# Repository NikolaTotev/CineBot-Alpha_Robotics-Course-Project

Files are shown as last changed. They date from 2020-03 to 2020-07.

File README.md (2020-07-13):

# Project Cinebot Alpha

This is the documentation for my Robotics Course Project created during my second year, second semester in FMI for the course Practical Robotics and Smart "Things".

<p align="center">
Robot_Full
</p>

## *Acknowledgements*
Before I begin, I would like to acknowledge my parents, for their constant love and encouragement, not only for this project but for all of my previous and current endeavors. Without them, this project would not be the same.
I would also like to thank the teachers of the teachers that guided me
through the skills I needed to learn to make this project a reality. In no particular order I'd like to thank:

* Dr. Ivan Chavdarov, for teaching me the skills related to 3D modeling & printing, as well as giving me guidance on my structural design by telling me what could be improved and how such things are usually made/designed.

* Trayan Iliev, for expanding my horizons on the subjects of IoT and the software side of robotics.

# Contents
-  [Introduction](#Introduction)
	* [Scope](#Scope)
	* [Key features](#Key-features)
	* [Initial design decisions](#Initial-design-decisions)
	* [Interesting Statistics](#Project-Statistics)
	
* [Getting started ](#Getting-started)   *(click here if you just want to setup the robot and learn how to use it)*
	* [How to run client](#How-to-run-client)
	* [How to run  server (robot)](#How-to-run-the-robot)
		* [Publishing from Visual Studio](#Publishing-from-Visual-Studio)
		* [Uploading via WinSCP](#Uploading-via-WinSCP)
		* [Running Server](#Running-server)
	* [Trouble shooting](#Troubleshooting)

-  [Hardware](#Hardware)
	* [Design constraints](#Design-constraints)
		* [Actuators](#Actuators)
		* [Method of manufacturing](#Method-of-manufacturing)
			* [Manufacturing capabilities](#Manufacturing-capabilities)
			* [Material choice](#Material-choice)
		* [Assembly methods](#Assembly-methods)
		* [Other resource constraints regarding hardware development](#Other-resource-constraints-regarding-hardware-development)
	
	* [Hardware design decisions](#Hardware-design-decisions) 	
		*	[Structure overview](#Structure-overview) (part evolution and motivation behind the design)
			*	[Base & base drive train](#Base-and-base-drive-train)
			* [Arm section](#Arm-section)
			* [Arm joint](#Arm-Joint) 
			* [Counter balance](#Counter-balance)
			* [Gimbal](#Gimbal)
			* [Limit switches](#Limit-switches)
			* [Electronics housing](#Electronics-housing) ***(design aspects)***
			
		* [Electrical system](#Electrical-system)
			* [Schematics](#Schematics)
			* [Used components](#Used-components)
			* [Electronics housing and connections to robot](#Electronics-housing-and-connections-to-robot)
					
-  [Software](#Software)
	- [Software Requirements](#Software-Requirements)
		- [Safety requirements](#Safety-requirements)
		- [Required modes of operation](#Required-modes-of-operation)

	- [Software Architecture](#Software-Architecture)
		- [Unix Domain Sockets](#Unix-Domain-Sockets)
 	- [Choosing a suitable platform](#Choosing-a-suitable-platform)
	- [Programing language selection](#Programing-language-selection)
	- [Diagrams](#Diagrams)
		- [System Modules](#System-Modules)
		- [Deployment Structure](#Deployment-Structure)

---
# ==== Disclaimer ====
This project is for ***educational purposes only***. This is my ***first*** robotics project and there are certainly bad practices/decisions that could lead to injury or damage to components.
If you decide to recreate this please do so carefully. If any issues are discovered please put in an issue so I can fix it.

_Also please note, this project is made by a beginner, I have never assembled, designed or programmed a robot before. When giving feedback or grading this please consider this._

---

# Introduction
## Documentation structure
This project has two main sections hardware & software. The structure of this documentation begins with the hardware aspects of the project because that is the way the development of this project began. After that, I will continue with the software side of this project.

 The goal of this documentation is to inform the reader about the project and give him/her a better understanding of the project, what the motivations are behind the various design decisions and how the many hardware and software components interact with one another to create a complete robot as well. This document will also cover the many mistakes I made along the way, the challenges I faced as a complete beginner, how I overcame them. I also describe the lessons I learned along the way and point out the improvements that can be made if someone attempts to recreate this project.

Since this is my first project and documentation of such a scale I would like the reader to know that there may be some errors and things that can be done better. If you find such a thing, please make an issue in Github so I can get some constructive feedback and so I can improve this project for future readers.

For the reader's convenience, I have added “Back to top” links throughout the documentation, they will lead you to the beginning of the contents page if you wish to read another part of the documentation.

## Scope
Since this is my first robotics project, the scope of this project is fairly limited if compared to the current state of robotics, but quite broad for a complete beginner.  At the start of this project the scope was quite limited, but as the development progressed so did the scope because I discovered new things that would help me improve this project and teach me even more new things. I have more things I’d like to add in the future, I would also be very happy if this could be used as a beginners project for students or just people who want to get into robotics. That is why this will be a 100% open-source project so anyone can contribute.

During the development of this project in no particular order I wanted to:

* Learn about the platforms that are available for robotics and that are suitable for beginners but at the same time have enough room for growth in the future
* Using 3D modeling for visualizing the robot and as a key component in the manufacturing phase.
* Exploring different methods of creating the physical structure of the robot.
* How actuators are made/chosen and how they are controlled
* Learn more about key principles about robotics such as
               * Kinematics
               * How to deal with forces/balancing issues
               * Safety considerations when designing a robot
               * Motion smooth / using the quintic polynomial equation to manage forces on the robot caused by acceleration during movement.
* Learn how to make a basic multithreaded control software for the robot
* Facial tracking using OpenCV and implementing a PID controller to track a face by moving the robot.

## Key features
* __Jog Mode__
This is manual control done via the encoders on the front of the electronics case. This is used for diagnostics and testing. This mode also shows off the multithread stepper motor control.

* __Program Path__
Similar to jog mode when it comes to controlling the robot, but there is an option for entering a node for a given position of the robot (both for gimbal and stepper motors). Once the wanted path is done, it is saved to a file and it can be replayed later using replay path mode.

* __Replay Path__  
Reads instructions from the selected file and replays them. A picture is taken at each node.

* __Face detection & tracking__
This mode is still a bit experimental, but it does detect a face using OpenCV with Haar Cascade. Then with a PID Controller, it tracks a face attempting to keep it centered in the frame. I followed [this tutorial](https://www.pyimagesearch.com/2019/04/01/pan-tilt-face-tracking-with-a-raspberry-pi-and-opencv/), but I had to make a couple of changes to make it work with the C# code. More information can be found in the [Unix Domain Sockets](#Unix-Domain-Sockets) section.

## Initial design decisions
The first choice I had to make was what kind of robot would be suitable for this project. The two main choices where either a mobile robot or a stationary robot arm. I know there are more options but considering my limited knowledge at the beginning I wanted to attempt one of the two types. In the end, I decided to make a stationary robot arm for the following reasons:

1. Work environment - Before and after the pandemic my work environment was limited and setting up an environment for a mobile robot would have impractical. For a stationary robot, it was much easier to designate one small spot for it,
2. Powering the robot - I only knew about lab power supplies and how they are used for such experimental projects, based on the knowledge my only reasonable option was a stationary robot as a mobile one would required batteries to operate freely.

Once I decided what kind of robot I would make the size of the robot was the next decision. Since I have a limited work area and limited resources such as time, money, and manufacturing capabilities I decided to make a fairly small robot arm that doesn't have practical use but is perfect for educational purposes.

Before beginning with the CAD design, I used Legos to create a crude model of the robot arm and the joints it would have and how they would move. I found this to be the best way to make the initial prototype as it cost nothing and gave a good enough visualization/feel.

## Project Statistics
* Work time - about 600-650 hours - aprox. 25-27days
* Print Time - 805h 8min - aprox. 33.5 days
* Total Project - 5.61GB

## Tools & Software
As this project has both software and hardware components I feel that it is necessary to list all of the tools I used during development

Hardware tools
- 3D Printer - Flashforge Creator Pro
- X-ACTO Knives
- Various screwdrivers
- Various pliers
- Clamps
- Soldering Iron
- Digital Caliper
- Wire-stripper

Software tools
- Visual Studio 2019
- Autodesk AutoCAD 2020 (Student Edition)
- Wolfram Mathematica
- Github Desktop
- WinSCP
- .NET Core IoT Libraries
- Flashprint (Slicer)

##### [Back to top](#Contents)

# Getting started
If you intend to build this robot, or even better, have already built it, this section is the one for you! The setup process isn't as straightforward as I would like, but considering the limited time, I think this is pretty good.
The system is divided into two parts
* Client
* Server
The server runs on the Raspberry Pi and the Client *(console version)* runs on any Windows or Linux machine.

## Prerequisites
Here are a couple of things you will need to get started:
* [Visual Studio 2019](https://visualstudio.microsoft.com/vs/community/)
* [WinSCP](https://winscp.net/eng/download.php)
* Basic Linux knowledge & ability to work in a terminal
* Command prompt or an SSH client such as [Putty](https://www.putty.org/) or [Solar Putty](https://www.solarwinds.com/free-tools/solar-putty) if you want a better GUI
* A raspberry pi with the latest version of [Raspbian](https://www.raspberrypi.org/downloads/raspberry-pi-os/) (or as it is now called "Raspberry  Pi OS)*
* [ .NET Core](https://github.com/dotnet/iot) needs to be installed on your raspberry
* You will also need to install [OpenCV](https://qengineering.eu/install-opencv-4.3-on-raspberry-pi-4.html)
#### For the builders
* If you are starting to build this, I suggest looking at the [Fritzing connection schematics](https://github.com/NikolaTotev/Robotics-Course-Project/tree/master/Documentation/Schematics)
* The [parts list](#used-components) is also something useful as well as the [STL Files](https://github.com/NikolaTotev/Robotics-Course-Project/tree/master/STL%20Files) may be useful for 3D printing.

## How to run client
I will describe how to run the client on windows, as that is the platform I have tested it on, but if you use the same steps used for [publishing the server](#publishing-code-from-visual-studio) you will be up and running in no time!

1. Once you have cloned or downloaded the repo, navigate to
` Robotics-Course-Project > Robot Code > Robot_Code`
and locate ` Robot_Code.sln` and launch it in Visual Studio.
2. When everything is loaded:
               * if you want to use the `GUI Client`,  find `WindowsClientGUI` in the *solution explorer* and run it
               * if you want to use the `Console client` locate the ConsoleClient in the *solution explorer*
3. After that just press `Ctrl+F5` to run

***[Helpful tip ]:*** 
*If you are new to Visual Studio, if the solution explorer is not visible you can search for it in the "Search" bar at the top of the IDE*

## How to run the robot

### Publishing from Visual Studio

***1. Locate the `Central_Control` project in the *solution explorer****

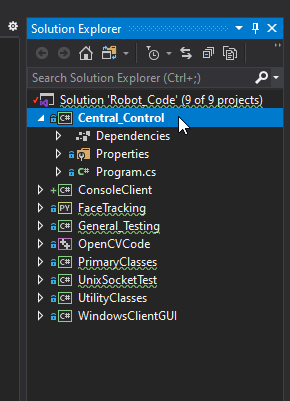
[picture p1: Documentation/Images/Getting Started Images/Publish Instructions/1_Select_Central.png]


***2. Right-click and find the `Publish` option.***

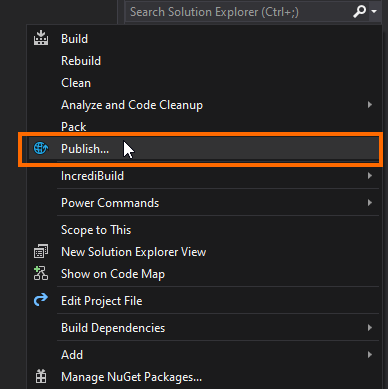
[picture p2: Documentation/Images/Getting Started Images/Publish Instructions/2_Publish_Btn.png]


***3. Once you press it, you will see this screen. Select the `Folder` option. Press `Next`***

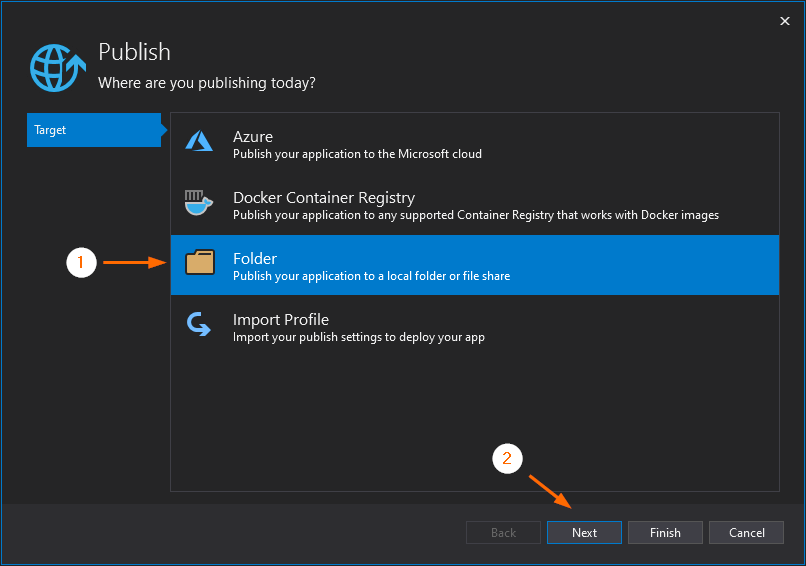
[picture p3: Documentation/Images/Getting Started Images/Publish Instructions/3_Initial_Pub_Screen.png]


***4. Select the desired publish path. Make sure it is easy to find since you will use it when [uploading via WinSCP](#Uploading-via-WinSCP). Press `Finish`***

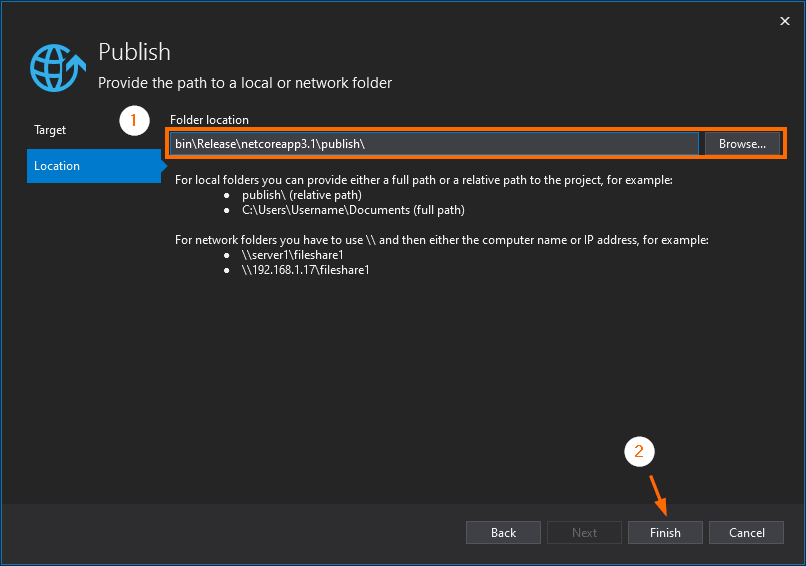
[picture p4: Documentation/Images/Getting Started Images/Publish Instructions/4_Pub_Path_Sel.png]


***5. You will now see this screen. Before publishing the configuration needs to be edited. Press the edit button.***

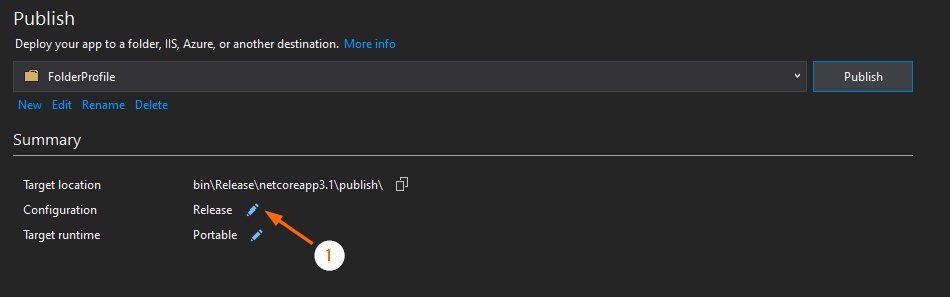
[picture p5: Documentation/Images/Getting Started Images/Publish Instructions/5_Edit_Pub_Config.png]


***6. This window will open and here you need to change the `Deployment Mode` and `Target Runtime` if you don't, it will not run on the Raspberry Pi.***

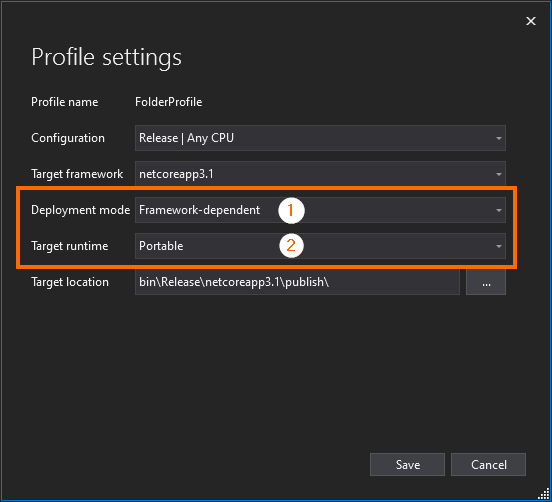
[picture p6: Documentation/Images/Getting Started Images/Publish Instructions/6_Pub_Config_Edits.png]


***7. `Deployment Mode` must be set to `Self-Contained`***



***8. `Target Mode` must be set to `Linux-arm`***

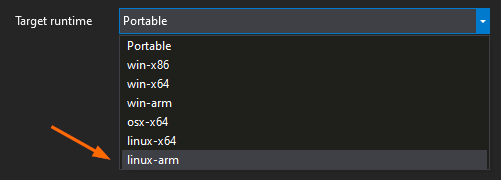
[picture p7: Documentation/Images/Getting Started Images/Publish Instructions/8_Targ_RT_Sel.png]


***9. The configuration window should look like this once you are done.***

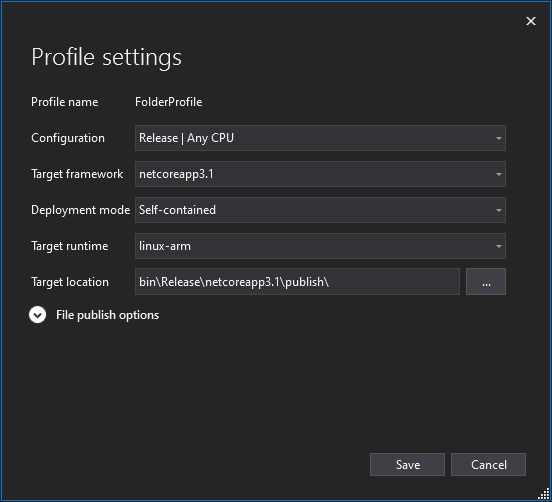
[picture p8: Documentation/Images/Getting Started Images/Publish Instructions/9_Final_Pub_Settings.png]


***10. After that, you are ready to publish by pressing the `Publish` button.***

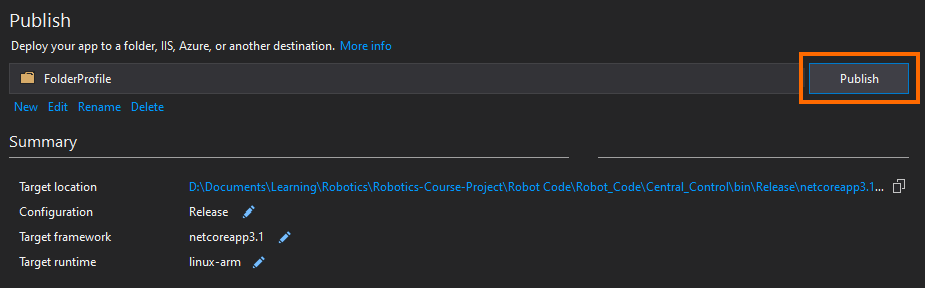
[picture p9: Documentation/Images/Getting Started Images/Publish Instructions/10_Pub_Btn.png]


***11. This is how the output should look like if everything has been published correctly.***



##### [Back to top](#Contents)

---
### Uploading via WinSCP
This section will not cover how to setup WinSCP, but it will show the basic upload procedure.

***1. On the RPi create a directory mine is `/home/pi/Documents/Robot_Code/Central_Control` In WinSCP navigate to that directory (the right section of the UI). 
On the left side navigate to the publish directory you set in the [publish guide](#Publishing-from-Visual-Studio).***

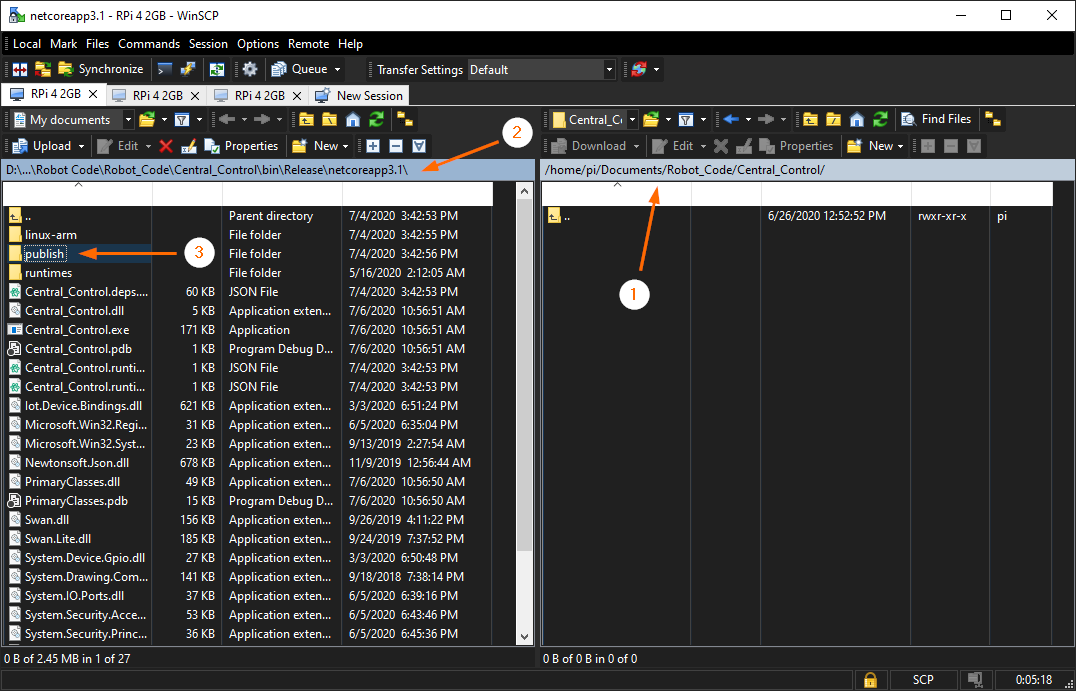
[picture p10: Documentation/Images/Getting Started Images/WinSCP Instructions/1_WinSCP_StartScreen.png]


***2. Select the publish folder and locate the `Upload` button. Then press it.***

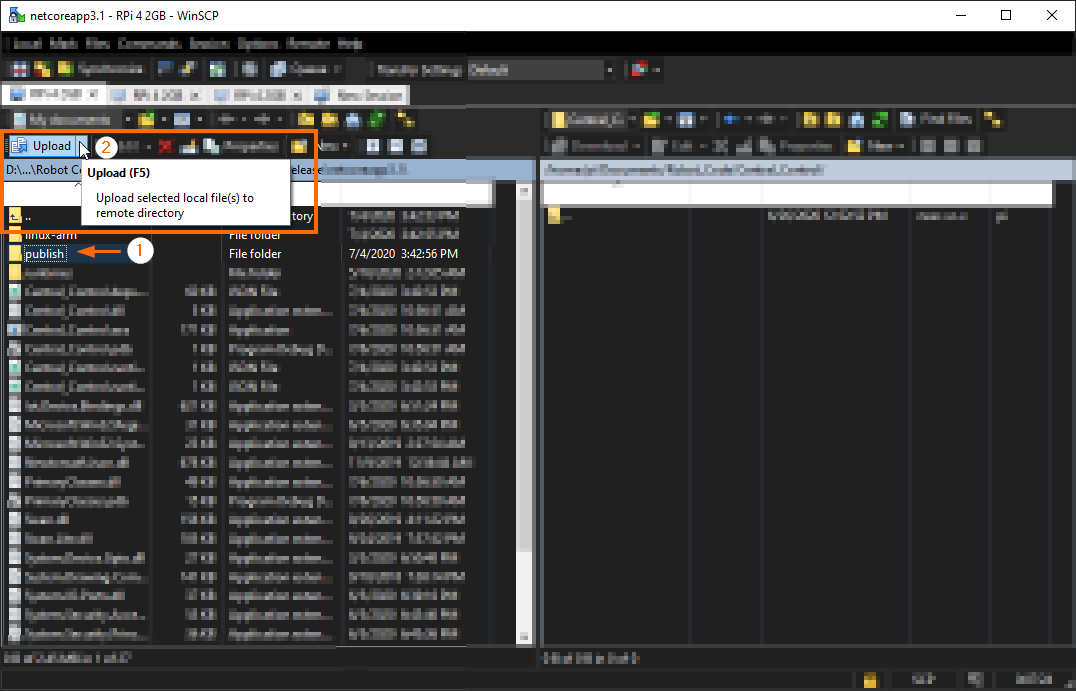
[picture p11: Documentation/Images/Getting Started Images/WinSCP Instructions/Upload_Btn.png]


***3. You will see the following screen, just press `Ok`***

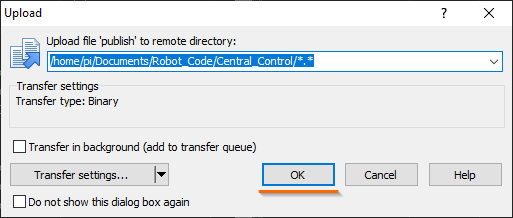
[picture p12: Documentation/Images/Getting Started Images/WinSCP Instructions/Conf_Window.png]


***4. Then you will see this window, I suggest setting the upload speed to `Unlimited` if it isn't already.***

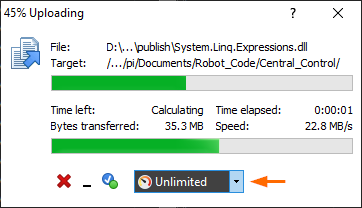
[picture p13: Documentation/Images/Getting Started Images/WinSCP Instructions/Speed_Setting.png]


***5. Once uploaded the UI should look like this.***

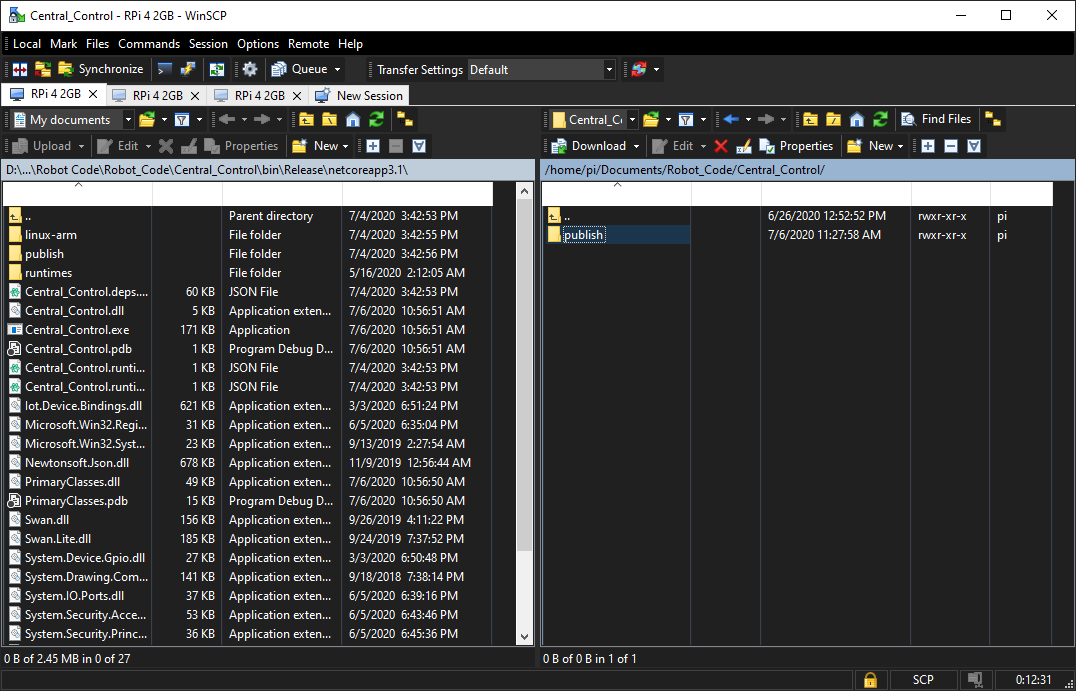
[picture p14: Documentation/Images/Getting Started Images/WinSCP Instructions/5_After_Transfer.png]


***6. Now it is time to set the correct permissions. Open the publish folder and locate `Central_Control`***

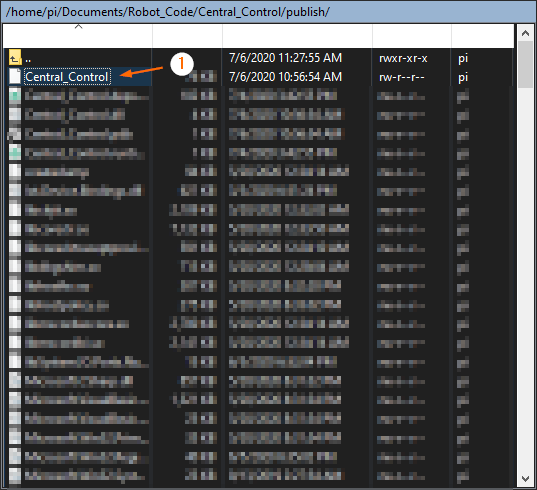
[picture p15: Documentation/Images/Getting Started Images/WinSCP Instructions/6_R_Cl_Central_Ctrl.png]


***7. Right-click and press the `Properties` option.***

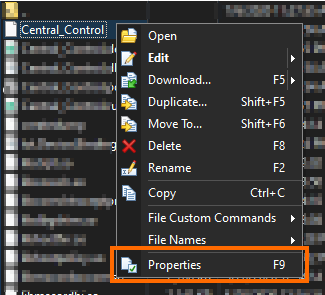
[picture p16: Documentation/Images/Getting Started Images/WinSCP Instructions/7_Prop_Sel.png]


***8. For simplicity, just check all of these boxes.***

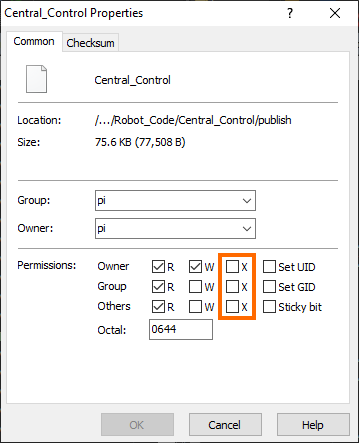
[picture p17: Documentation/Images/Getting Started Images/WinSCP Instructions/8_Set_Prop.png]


***9. Press Ok and you should be all set to run the server!***

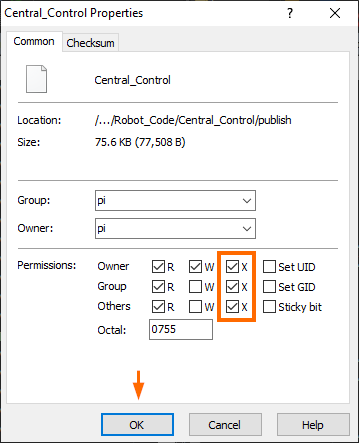
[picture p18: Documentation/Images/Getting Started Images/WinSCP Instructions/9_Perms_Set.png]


##### [Back to top](#Contents)

---
### Running Server
***1. Login to the Pi via SSH (you can also use a monitor or keyboard, SSH is just a bit more convenient)***

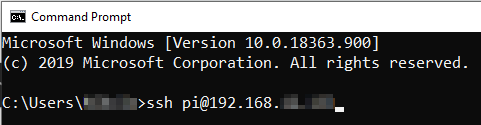
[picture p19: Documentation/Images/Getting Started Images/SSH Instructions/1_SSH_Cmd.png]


***2. Enter your password***

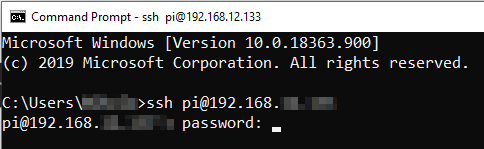
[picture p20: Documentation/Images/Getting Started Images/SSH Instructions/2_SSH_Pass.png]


***3. Navigate to the directory containing the program***

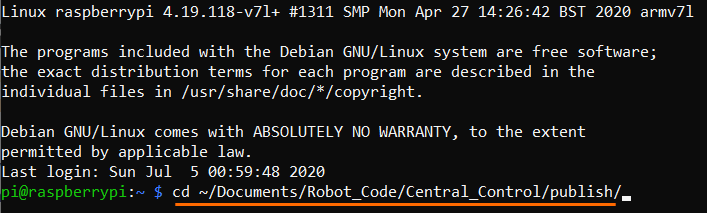
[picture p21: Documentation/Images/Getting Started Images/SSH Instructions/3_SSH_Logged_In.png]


***4. Start the program***



***5. If everything has started correctly, you should see this message:***

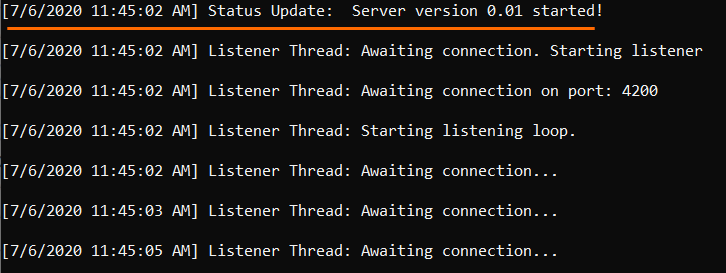
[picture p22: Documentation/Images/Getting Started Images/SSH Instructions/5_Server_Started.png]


 and you should see the notification LED's blinking like this:



### Troubleshooting
Some known errors may occur during the starting of either the server or client.
1. Arduino is not plugged in. This error looks like this and can easily be fixed by ensuring the Arduino is plugged in.

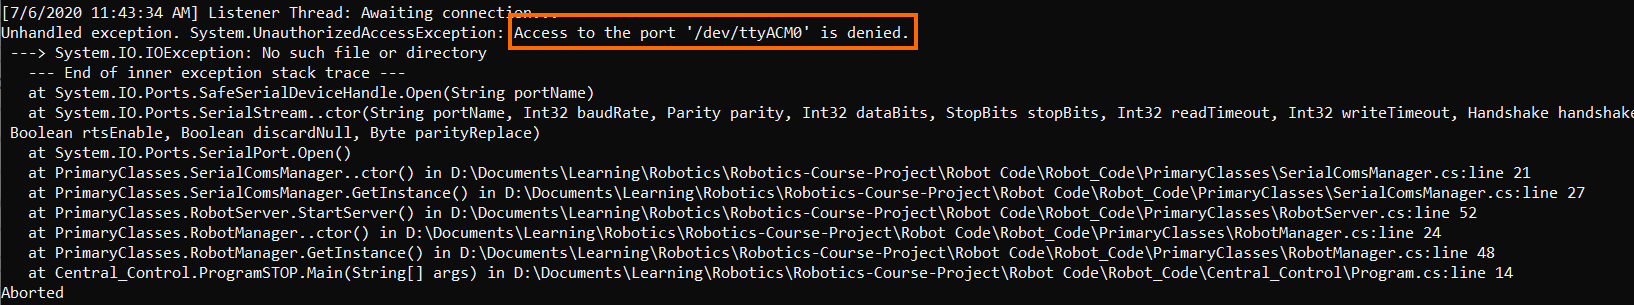
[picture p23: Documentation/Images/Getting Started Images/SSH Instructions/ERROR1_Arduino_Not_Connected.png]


##### [Back to top](#Contents)

---

# Hardware

## Design constraints
This section covers the design constraints I had during the development of the hardware and how the constraints affected the final design.

### Method of manufacturing
Since this project requires are higher accuracy of the parts and since I had limited time to make each part myself I decided that the best option would be to utilize 3D printing to make all of the parts for the robot. Since I also enrolled in a 3D modeling course in the same semester, the decision to use 3D printing would mean that I could apply the from one course in another.

#### Manufacturing capabilities
The printer I chose for this project as mentioned in the tools section is the Flashforge Creator Pro. Since it was my first printer I decided to go with this model because it has dual extruders and the ability to print in a variety of materials, giving me enough options for the future.

#### Material choice
Because all of the printing would be happening in my room, I decided to go for **PLA** as it does not emit toxic odors and it is significantly easier to print with. The strength of the material is adequate and is suitable for relatively small forces involved.

---

### Actuators
For the primary actuators, I decided to use two NEMA 14 35x28 stepper motors and for the gimbal actuators, I use two micro [servos with metal gears]([https://erelement.com/servos/feetech-ft90m](https://erelement.com/servos/feetech-ft90m)) for the rotate and tilt axes and a [larger servo with plastic gears ](https://www.robotev.com/product_info.php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) for the pan axis.

*Due to lack of knowledge at one stage of the project I had to change the stepper motors from my initial NEMA 14 35x26 to the slightly more powerful 35x28. That said, I believe it is possible to make this project work with the smaller motors but better gearing would be required*

Since these motors lack the holding torque to hold the arm of the robot horizontal or to even lift it, [reducer mechanisms](#Reducer-mechanisms)  had to be implemented

---

### Assembly methods
As I am using 3D printing for making all of the parts I need to take into account the weaknesses and strengths of additive manufacturing to print good parts.
Most of the parts are printed in a way that avoids overhangs as much as possible. Layer orientation is taken into consideration when possible.

To assemble all of the parts I use two main techniques:
- M3 & M2.5 machine screws of various lengths.
- Trapezoid wedges that slide into each other

The combination of these two methods allows for a good balance between the solid assembly of large modules and allows those modules to be connected using a universal attachment interface.

<p align="center">
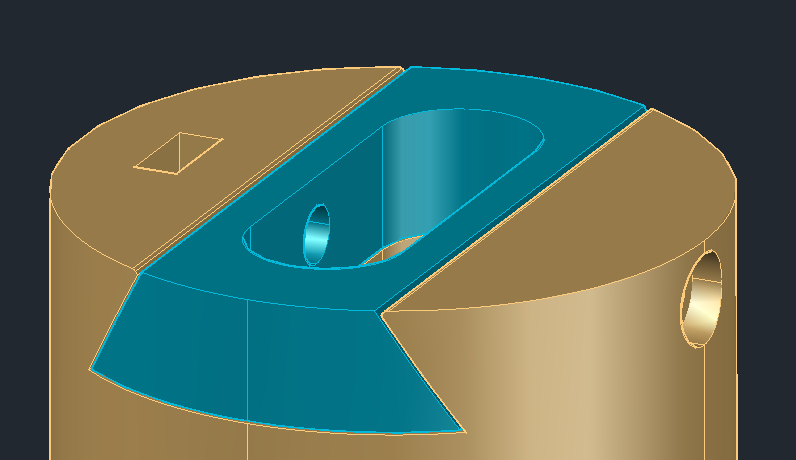
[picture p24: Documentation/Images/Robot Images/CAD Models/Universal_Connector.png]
            
</p>

***Note:*** Initially I used two other methods of assembling the robot:
1. Friction fit connections with a square or hexagonal shape to allow for easy assembly/disassembly.
2. Screws for all of the connections.

Both of these methods had significant downsides. The friction fit relied on tight tolerances, something that is not consistent when 3D printing parts.
For the screw method, once the larger parts were connected, if something needed to be replaced, a significant amount of work needed to be put in to change a single part.

##### [Back to top](#Contents)
## Hardware design decisions
### Structure overview
The structure of the robot is fairly simple. In the following points, I'll describe each part and all of the iterations I had to go through. The general goals for the hardware can be divided into two sections:

* Robot structure
	1. It has to be printable
	2. The parts need to be able to support the expected forces and use as little material as possible
	3. The reducer mechanisms need to move smoothly
	4. As mentioned above assembly needs to be pretty simple
	5. Parts must be modular and easy to swap out
	6. Built-in cable management.
	7. It needs to look good (this has a lower priority, but still an important aspect)
               
* Electronics housing
	1. There must be enough room to work inside and fit the electronics
	2. Cooling needs to be integrated into the case to help with performance
	3. Notification LEDs need to be in a good position for the user
	4. Any controls such as rotary encoders also need to be in an easily accessible spot.
	5. All ports that are used for connection to the robot need to be in the back
	6. As with the robot, it has to look good (again lower priority)

*Some of the things mentioned in the electronics housing are described in more detail in the [electrical system](#Electrical-system) section.*
####  A little bit about iterations
I have decided to go through all of the iterations because I think it is important for me to show the whole process. That way I can describe the things I've learned along the way and it is a great section for beginners to see the mistakes I've made so they don't make them as well.
Since this is quite a lengthy section I will provide skip links so that you can only see the final design or so you can skip directly to the [software part](#Software) of the project.

---

####    Base and base drive train
Since this is a stationary robot, the base is a key part of the design and a good base is essential for the overall stability of the system. This section also experiences the most loading and has to be designed with that in mind. I also want to cover the different adapters that are used to connect the arm sections to the base subassembly.
* ___Base & base drive train iterations___

<p align="center">
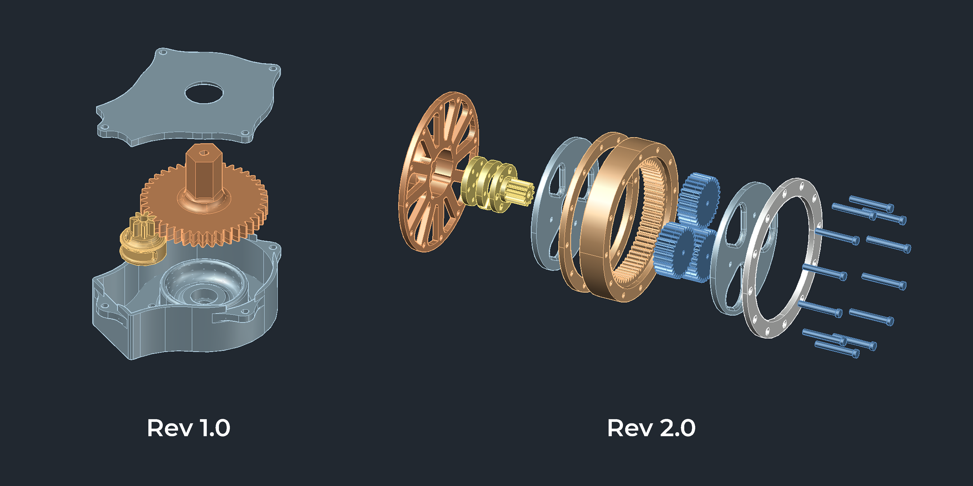
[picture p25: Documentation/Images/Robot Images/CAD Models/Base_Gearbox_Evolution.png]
Base_Gearbox_Evolution
            
</p>

* __Iteraton 1__
Initially, I started with this design. As you can see it is a simple and small gearbox and the larger gear has a hexagonal shaft. and it sits on a stand. The idea behind this was to have the rest of the robot be friction fit onto it, however, there were many tolerance issues. Another significant issue with this base, it had a small footprint and once the robot was friction fit ontop  there was a lot of wobbling around and I abandoned the idea.

* __Iteraton 2__
This iteration was inspired by the first version of the arm joint planetary gears and then a smaller version of this base gearbox was used in the final iteration of the arm joint. In theory, this setup should've been much more stable, but the way I chose to attach the base adapter created a lot of problems. This gearbox also had some binding issues in some spots, which resulted in irregular motion and the stepper motor losing steps. The problems mentioned along with the arm section issues at the base of the robot made me rework the entire base.

* __Iteraton 3__
This is the final iteration. As you can see it quite different and uses a much simpler and adjustable drive train. In the base, there are 2 75 mm *(outer diameter)* bearings that provide the structural stability and smooth rotational movement. This base fixes all of the issues that the previous ones had and helped solve the issues with the base arm section

**Thigs I learned** - Its best to keep reducer mechanisms as simple as possible. It is important to consider the forces that will be exerted on a part, especially on the base of the robot. Bearings are something that should be used more often, they significantly improve the final result and are a great addition to 3D printed mechanisms.
               
##### [Back to top](#Contents) 

---          
               
* ___Base Adapter iterations___
   This will just quickly cover the different adapters I made.

<p align="center">
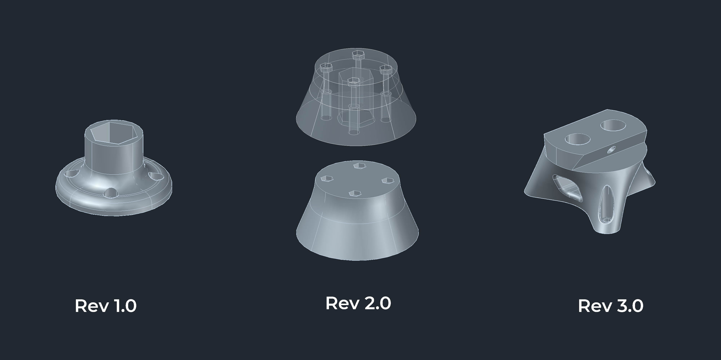
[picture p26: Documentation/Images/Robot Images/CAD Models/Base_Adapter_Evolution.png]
Base_Gearbox_Evolution
            
</p>

* __Iteraton 1__
 Uses hexagonal friction fit on one side and screws for mounting the arm section.
Cons -
	* No cable management
	* Tolerance issues
	* Time-consuming to mount/unmount arm sections
	* Too thin for the loads it would experience

	Pros -
	* simple design
	* quick to print.

*  __Iteraton 2__
               This version as you can see it a bit better, but it still has the major issues of the previous one. 
               
      Pros -
      * fixes thinness issue
      * adds some stability due to wider footprint
      
      Cons
      * still time-consuming to mount arm sections
      * still has tolerance issues
                
* __Iteraton 3__             
               This one solves all of the issues of the previous ones but introduces some new ones. As you can see it is connected with screws to the gearbox, but those screws also hold the planet gears and carrier in alignment. This means that they can't be tightened too much as it will cause the gearbox to bind. Despite those problems, the easy swap functionality that comes from the use of a universal trapezoid mount allows for easy mounting of the other part of the robot. This base also has cable management that feeds the cables out of the back.
               
* __Iteration 4__
The final iteration of this part is removing it altogether. See the last arm iteration to understand the whole idea.

##### [Back to top](#Contents)
---

#### Arm section
This is the most important part of the robot. It makes up the majority of the assembly and without it, the robot would not work. This part also transmits the most load and has to be made both light and strong. Many iterations were needed to get to the final version.

<p align="center">
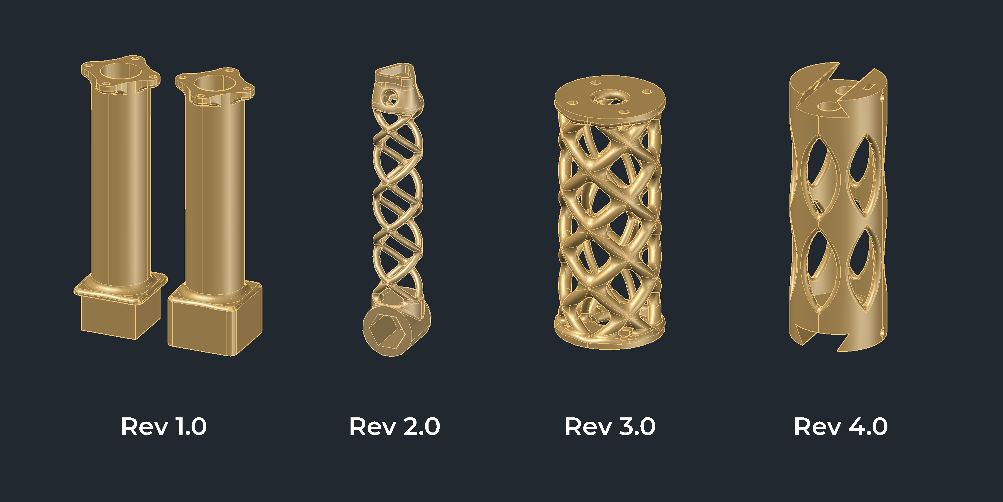
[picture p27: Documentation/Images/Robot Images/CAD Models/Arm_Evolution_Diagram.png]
Arm_Evolution
               
</p>     

* __Iteraton 1__
This was not thought through very well. As the previous first iterations, it relies on friction fits and too many screws to be practical.

* __Iteraton 2__
 This iteration is also poorly designed. While the shape is cool, it is too thin, too small and again relies on a friction fit.
   
* __Iteraton 3__
This version is a bit better, much stronger but still too small and once again it uses too many screws.

* __Iteraton 4__
This iteration is where better design choices emerge. There is proper cable management, it is light yet strong. Unfortunately, it is too complex and takes too long to print. It also uses too many screws.
                 
* __Iteraton 5__
This is the first iteration where a universal connector is used. The shape is simplified and there is better cable management. This design goes through 2 updates to make it stronger because it experienced a structural failure once. These updates just make the walls thicker.

* __Iteraton 6__
For this iteration, the top arm section is the same, but the base arm section has been reworked due to the structural failure shown below. This change also comes from the redesign of the base drive train. As you can see, it still keeps the universal connector, it is also much more stable, compared to the previous arm sections.

##### [Back to top](#Contents)
---          

#### Arm Joint
This part is the one and only "joint". I call it a joint because it connects two arm sections in a mobile way. This part of the robot had a couple of requirements to meet:
1. It needs to be strong enough (structurally) to lift the weight of the arm.
2. Since the stepper motor can't lift the arm on its own the joint needs to be some kind of reducer with an appropriate gear ratio. The gears must also operate smoothly.
3. It needs to implement a universal mounting system.

<p align="center">
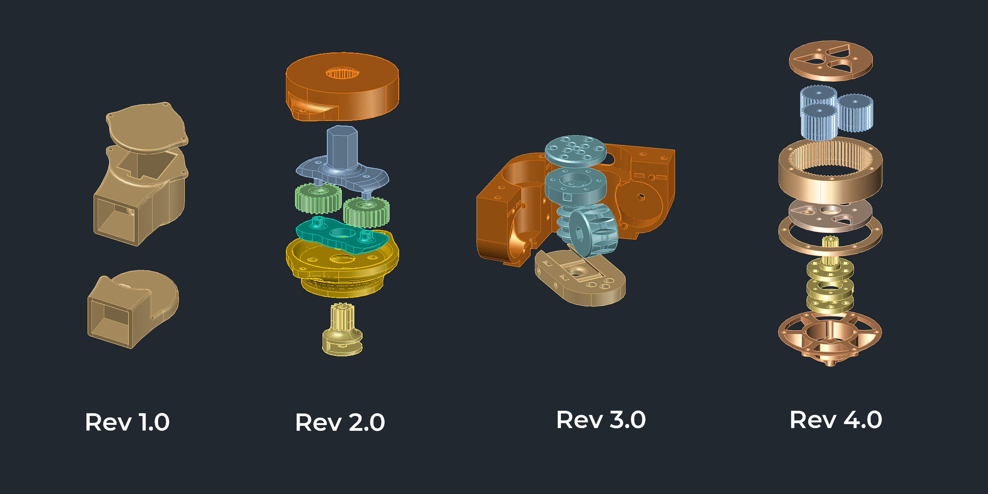
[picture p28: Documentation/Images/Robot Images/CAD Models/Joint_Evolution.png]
Arm_Joint_Evolution
                               
</p>

* __Iteraton 1__
 In the very beginning since I had never worked with stepper motors, I didn't know that they can't lift much on their own, and they require some kind of reduction mechanism.
This is why the first iteration has no gears whatsoever.
                 
 * __Iteraton 2__
This iteration uses a very simple planetary gearbox with a 7:1 reduction ratio. Was able to move the arm, but as it relies on a friction fit it is not stable. Along with those issues, after the gimbal iterations, it proved to be too weak.
                
* __Iteraton 3__
In this version, I decided to try to make a worm drive, but since it is a much harder reducer to make it had internal friction issues that caused it to be too weak.

* __Iteraton 4__
This is the final iteration and it is a smaller version of the second iteration of the base gearbox.  It shares its flaws, but they were not as pronounced due to the smaller forces exerted on it. Using this new gearbox allowed me to finally add the universal mounting bracket to it.

##### [Back to top](#Contents)
----

#### Joint to arm section interfaces/adapters
* __Iteraton 1__
               As you can see there is more than one version, but I'm grouping them as the first iteration as they do not include any counterbalance. These are simple, they all do their job, but due to the weight of the gimbal, a counterbalance is required.
               
* __Iteraton 2__
As you can see in this version, at the back there is a mounting point for the counterbalance mentioned above. This makes the job of the reducer much easier by balancing the forces.

##### [Back to top](#Contents)
---

#### Counter balance
* __Iteraton 1__
This part is pretty simple. Since I needed something to balance the gimbal, and an Arduino is needed to control the motors, I decided to combine the two and this is the result. The back has a tray for some metal weights and on the top, there are mounting holes for the Arduino. As mentioned above it connects to the second iteration of the arm joint adapter

##### [Back to top](#Contents)
---

#### Gimbal
<p align="center">
Gimbal_Full_Left
</p>

This part also has a lot of iterations, as initially, I didn't know what the best approach was. All of the axes are controlled via servo motors.

<p align="center">
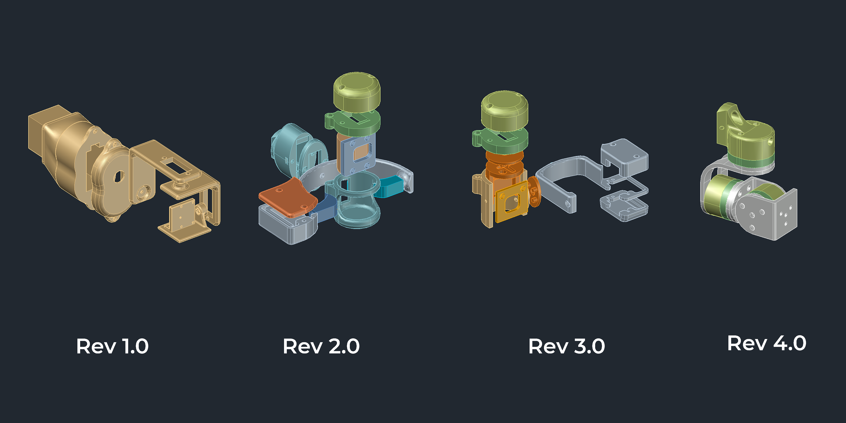
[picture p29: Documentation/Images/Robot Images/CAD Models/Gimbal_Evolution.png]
Gimbal_Evolution

</p>

* __Iteraton 1__
 This looks like a standard gimbal, the rotation motor housing is quite big and it is really heavy. Along with that, the camera mount is weak and the tilt and pan arms are also flimsy.

* __Iteraton 2__
The second version of the gimbal is very complex and rather large. Due to this fact, it is very unstable and I quickly abandoned it.

* __Iteraton 3__
The third version is inspired by the second one but attempts to minimize it by using smaller servos and smaller pieces. This design has major alignment issues. It is also very difficult to assemble and easy to break.

* __Iteraton 4__
This final design is inspired by [a project I found on youtube](https://www.youtube.com/watch?v=wQypj7ti7Vw). I was already behind schedule and I thought that it's time to look for some help. I had to make the models from scratch since I am using servo motors and the person in the video is using brushless gimbal motors.

##### [Back to top](#Contents)
---

#### Limit switches
<p align="center">
Limit_Switch
</p>

These don't have any iterations. I just bought a simple switch from the store and mounted it to the robot with two simple mounts. Despite their simplicity, these are critical parts as the allow the robot to "know" what position it is in. Please read [the improvements section](#Possible-improvements) for more insight on the improvements I would make in the area of positional awareness.

##### [Back to top](#Contents)
---

#### Electronics housing

<p align="center">
Electronics_Housing_Wide
</p>

This is a pretty simple part of the whole project. Its main goal is to make the project a bit more complete and polished. It also ensures, that once all of the cables are connected in working that they stay that way. The case also provides active cooling because it has two 95mm fans on one side.

***Possible improvements***
* This housing it a bit large for the number of components inside, but since it was my first attempt at such a thing, I decided to leave enough space to work inside.

* It also tends to tip forward as it isn't well balanced, so some legs or a flatter bottom might be a nice improvement.
* Internal cable management can be improved

* External cable management, such as ports for USB cables, ethernet, and so on. At the moment, all of those cables go directly out through the back opening. Ideally, it would have some sort of panel with the right kind of holes.
##### [Back to top](#Contents)

---

### Electrical system
#### Schematics
The schematics are very useful for anyone trying to make this exact robot. Please make sure to safely handle components and double-check connections before powering on the system. ***NEVER plug or unplug anything from the  RPi or Arduino while they are working. ***

* ___Stepper motor connection schematic___ [_alternate link_](https://github.com/NikolaTotev/Robotics-Course-Project/tree/master/Documentation/Images/Electronic%20Schematics)
<p align="center">
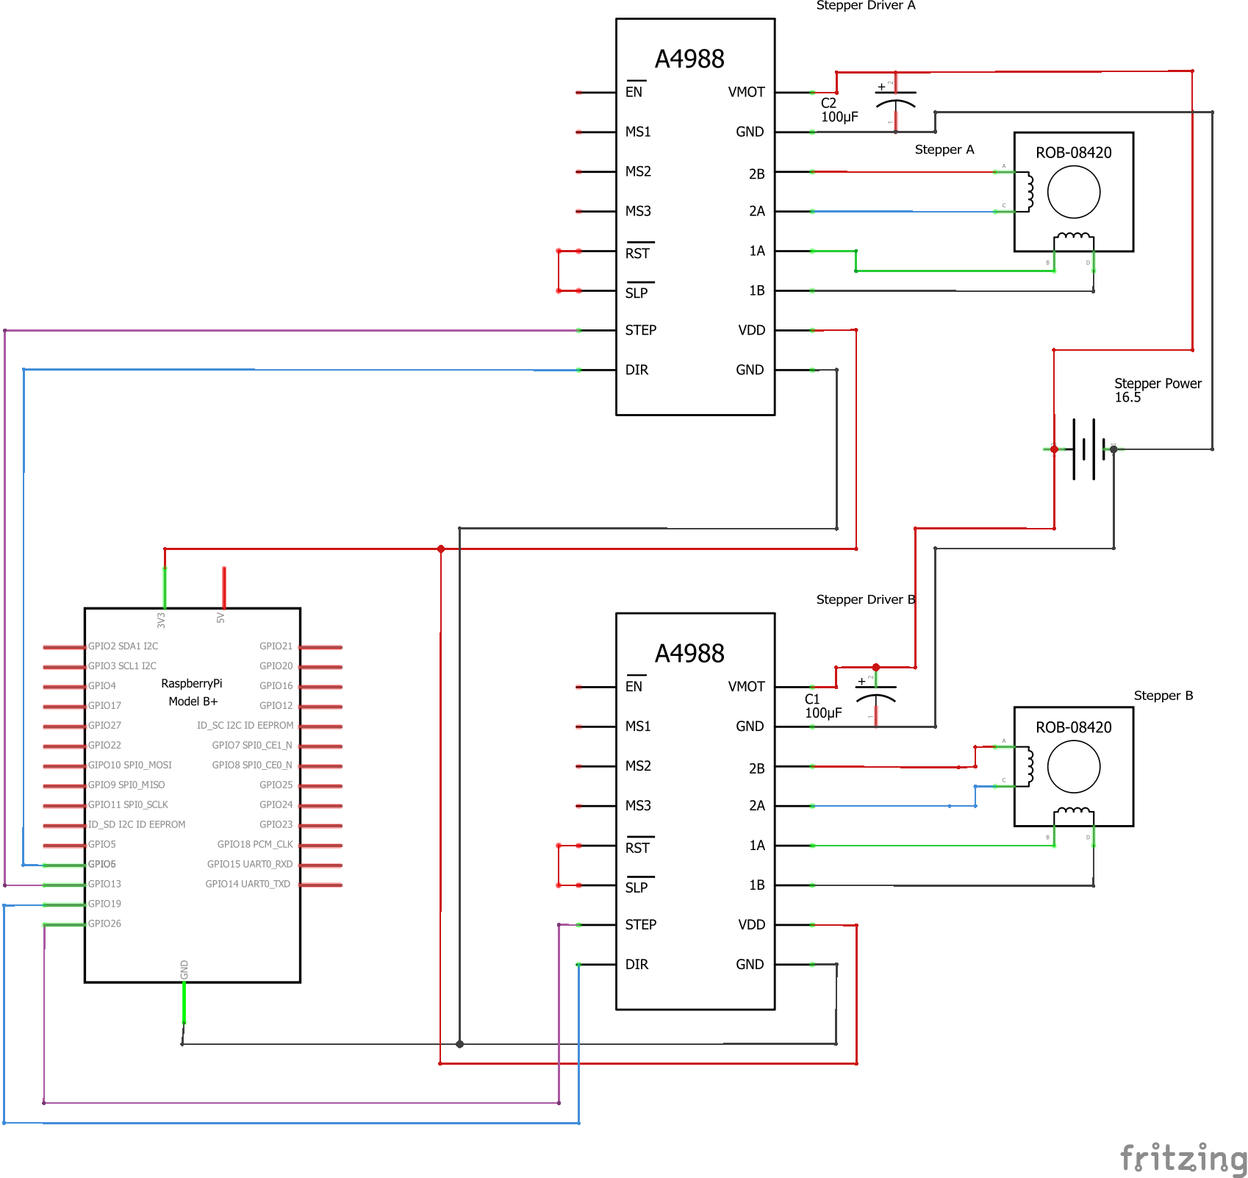
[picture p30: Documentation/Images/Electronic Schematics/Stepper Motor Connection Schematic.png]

</p>

---

* ___Encoder & switch connection schematic___ [_alternate link_](https://github.com/NikolaTotev/Robotics-Course-Project/tree/master/Documentation/Images/Electronic%20Schematics)

<p align="center">
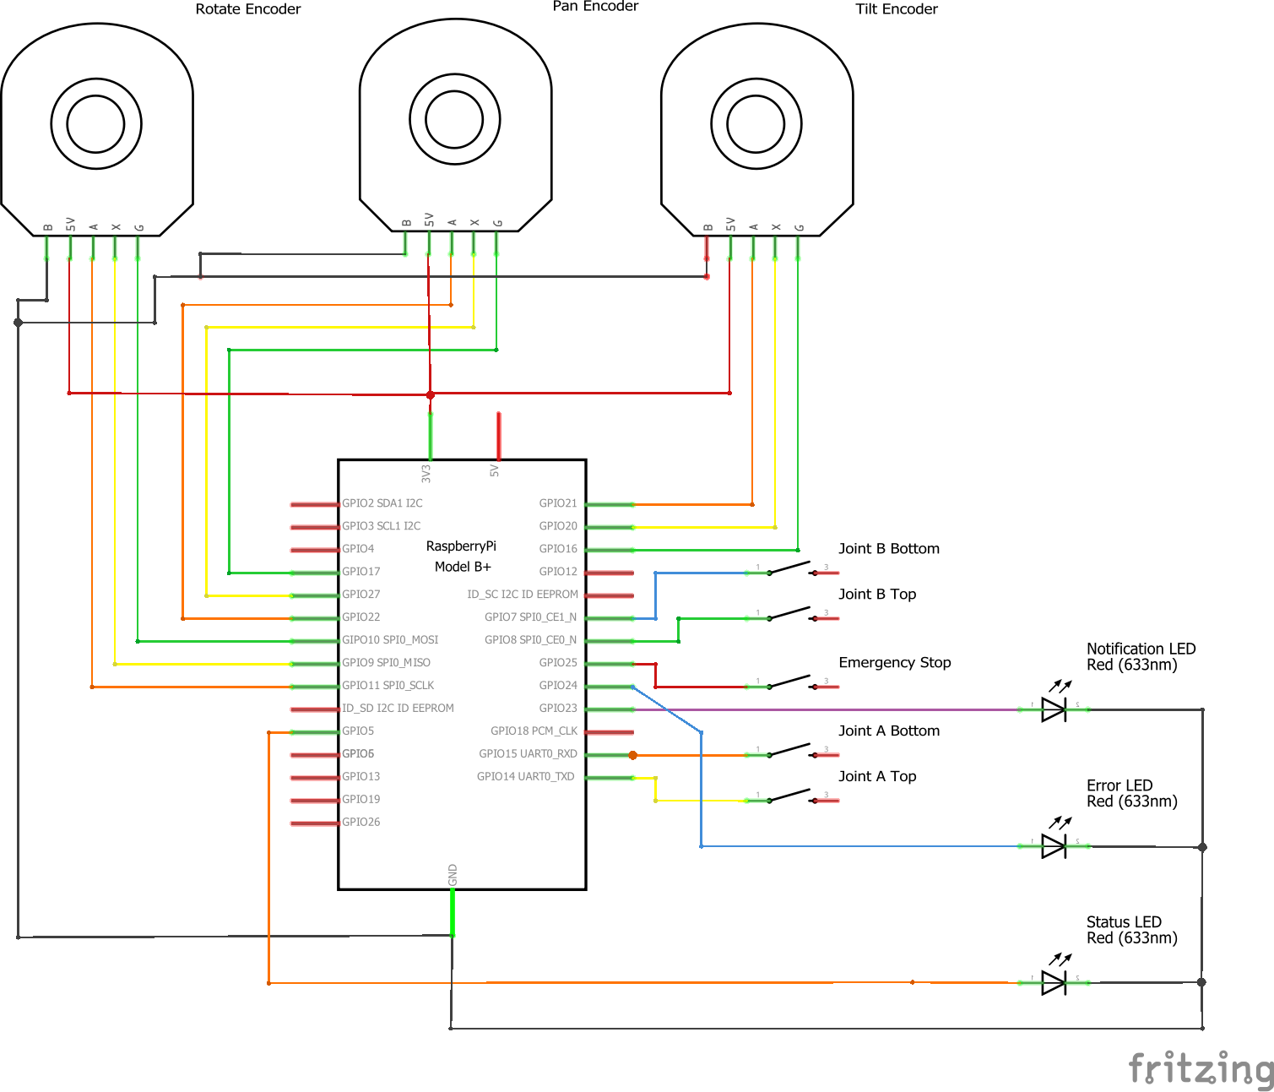
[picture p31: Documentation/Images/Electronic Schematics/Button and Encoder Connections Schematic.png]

</p>

---

#### Used components
* __Stepper motor & stepper motor drivers__
               * [A4988 Stepper Motor Driver Carrier](https://www.pololu.com/product/1182)
               * [NEMA 14 Stepper motor](https://www.pololu.com/product/1208)
* __Encoders__
               * [Waveshare rotary encoder](https://www.waveshare.com/rotation-sensor.htm)
* __Single-board computer & microcontroller__
               * [Raspberry Pi 4 2GB](https://erelement.com/raspberry-pi-4-2gb) is used as the primary computer.
               * [Arduino UNO](https://store.arduino.cc/arduino-uno-rev3) is used for servo control.

---

#### Electronics housing and connections to robot
The electronics housing is not an essential part of the project, but it makes for a more complete and polished project. It also hides the mess of cables and provides an interface for the robot to connect to via standard ports.

**There are 4 ports:**
1.  Stepper motor A
2. Stepper motor B
3. Servo power & limit switches for stepper A
4. I2C connection & limit switches for stepper B _(Unfortunately I2C is never used)_

<p align="center">

</p>

---

### Possible improvements
* Putting everything on one PCB
* Increasing modularity by using even more universal plugs for other components.
* Adding microstepping control to the stepper drivers
* Utilizing the available I2C connection.
##### [Back to top](#Contents)
---                          
# Software
The software is the other big component of this process. It is responsible for the safe control of the robot. It is also the bridge with which the user interacts with the system. This is why I want to begin with some of the requirements that I decided are important for this project.

---
## Software Requirements
### Safety requirements
Since this is a simple robot, with limited functionality, I decided to make safety features as part of the functionality of the robot. Two main safety features are noteworthy:

1. There is a physical emergency stop button that is monitored by processes that control the stepper motors or send commands to the Arduino via the serial port. If the button is switched on those processes immediately stop the movement and exit to a safe program state. This check is performed before any movement code is executed.

2.  There are physical limit switches that limit the motion of the robot and protect it from entering into dangerous positions. These are also monitored by the processes that perform movements. The difference is, that if a limit is hit, the robot can move back into a safe position if such a command is given.

These two safety-critical checks run on a separate thread and for each motor at the same time. All of that said, it is important to consider the [platform](#Choosing-a-suitable-platform) and [programing language](#Programing-language-selection) being used, and the pros and cons associated with those decisions.

### Required modes of operation
Along with the safety features, the robot has a couple of different modes of operation:
1. Simple jog mode - control one stepper motor at a time.
2. Multithread jog mode - control both stepper motors at the same time. 
3. Gimbal jog mode - control the gimbal - all axes at the same time.
4. Record path - records a path, multithread stepper motor control, and an option to switch to gimbal control. Path nodes are set by pressing the correct buttons for each mode. More info can be found in the [how to use section]()
5. Replay path - Reads a saved file and replays the motion that was recorded.
6. Face detection & tracking - track a detected face by attempting to keep it in the center of the frame  ***(only works for gimbal)***

### User interface
This is an important category, as it is the way for the user to know what mode the robot is in.
This is done via 3 LED's mounted on the front of the electronics housing. The main way the user can interact with the system with via the client application which has both a GUI and console interface.

<p align="center">

</p>

---

## Software Architecture
### Choosing a suitable platform
Due to my limited budget and experience, the most reasonable platform was the Raspberry Pi and the Arduino UNO. Considering my fairly light requirements these two devices are more than capable to meet the requirements and perform well.

### Programing language selection
My initial choice was Python, but it was lacking TCP pending functionality that prevents blocking of the main thread while the server awaits a connection. I am sure some options allow for this functionality, but I was not able to get something to work. This issue combined with my lack of Python experience made me look for alternatives.
Since I have previous experience with C# and since the Raspberry Pi is essentially running Linux my dad suggested that I look into .NET Core which can be run on Linux. After a bit of research, I discovered the .NET IoT Core library by Microsoft. It was easy to set up and quickly test and that is why the majority of the software is written in C#.

***Note:***
*1.  I am aware that C# is not the best language for a robotics project, but since I had so many other things to figure out, I decided that it was best to have at least one thing that I shouldn't worry about.*

*2. I am also aware of [ROS](https://www.ros.org/), but I found out about it too late into the project for it to be possible to switch.*
*3. Despite the cons, for this current project, C# is more than capable of delivering good performance. This has been determined by simply working with and on the system for 5 months*

## Unix Domain Sockets
As mentioned in the [Key Features](#Key-Features) section, there is a mode for facial tracking. The problem is that is written in Python, but all of my other code is in C#. This means that I need some way for the two processes to communicate with each other. Unix Domain Sockets to the rescue! Since everything is a "file" in Unix, I can just create a simple server-client set up to allow the Python program to communicate with the C# cod that controls the servos.

---

### Software motor control
This is a separate section because there is more to it than turning the motor on and off.
The standard way of moving a stepper motor with the `A4988` driver is by pulsing the step pin at a given speed. For simple applications, this is more than enough, but since this is a robot and since there is a considerable amount of mass that needs to be moved, simply moving the motor from 0 to full speed is not possible. There are a couple of  unwanted side effects of such instant acceleration:

* The stepper motor losing steps
* Extreme stresses that can lead to structural failures like this:
<p align="center">
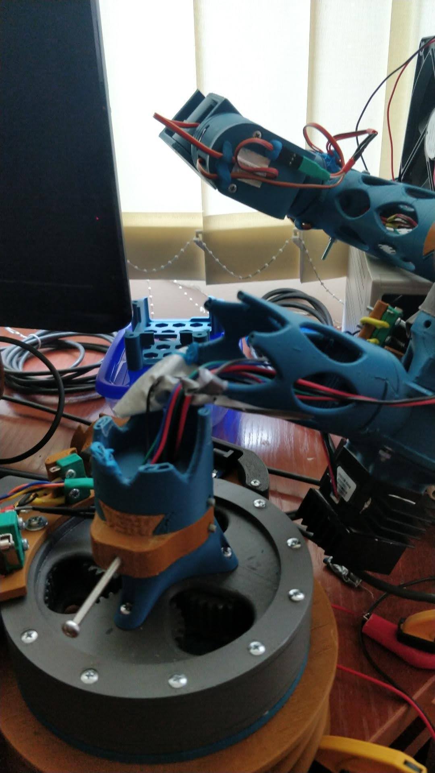
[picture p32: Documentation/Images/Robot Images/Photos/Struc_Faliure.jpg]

</p>

* Unnecessary wear on components.

A common approach that is used in larger robots is by using a [polynomial trajectory](https://www.youtube.com/watch?time_continue=8&v=HqQBL6xcj4w&feature=emb_logo) to ensure that the robot moves from one position to another smoothly over time. By using such a trajectory we can imagine the position, velocity and acceleration curves looking something like this:
<p align="center">
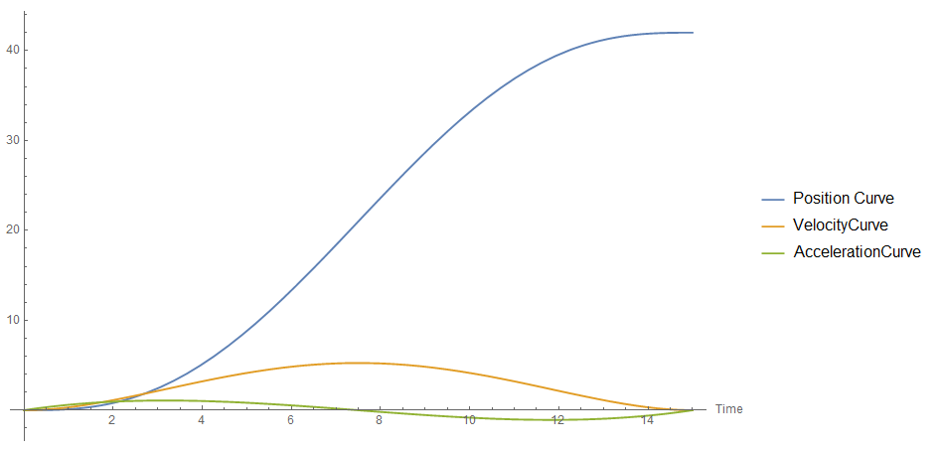
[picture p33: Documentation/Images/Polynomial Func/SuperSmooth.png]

</p>

This is done by using this kind of a quintic polynomial equation:

where the function itself gives us the change in position, the first derivative gives us the velocity curve and the third derivative gives us the acceleration curve. All of these curves are given for a set time period.

Let's imagine we want to rotate the base of the robot from 0 to 42 degrees. There are a couple of options:

If it takes ~ 0 seconds to move from 0 to 42 degrees, the curves would look something like this:
<p align="center">
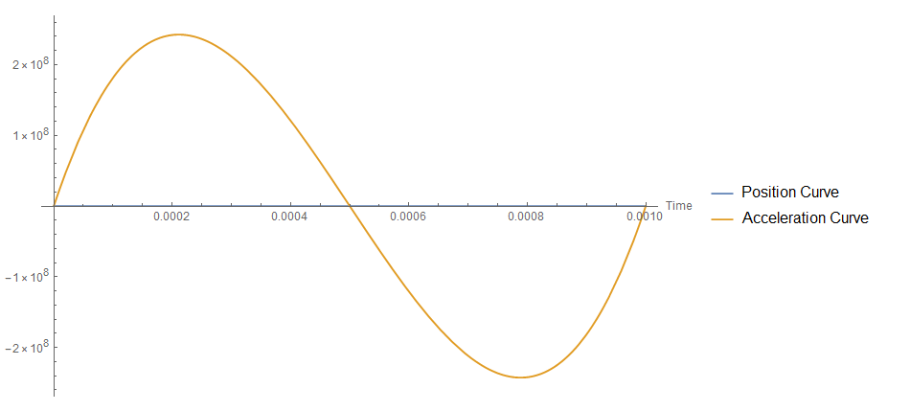
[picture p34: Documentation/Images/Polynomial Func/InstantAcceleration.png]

</p>

<p align="center">
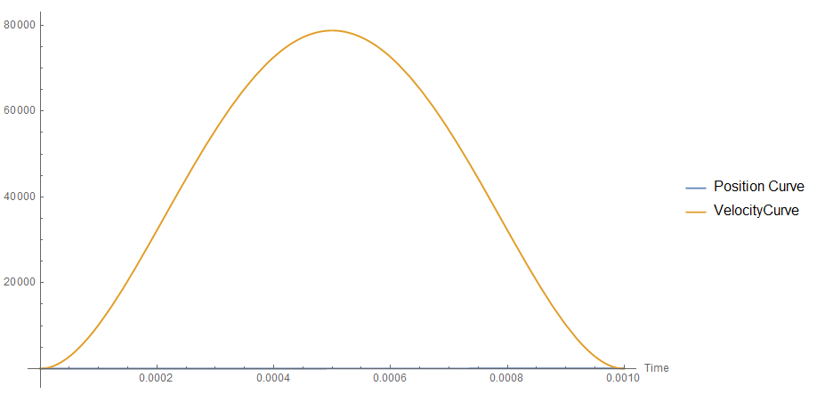
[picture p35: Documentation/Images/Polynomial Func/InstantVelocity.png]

</p>

***Note: The Y-axis values are the value from the function and do not represent actual velocity or acceleration metrics***

As you can see, both acceleration and velocity almost instantly shoot up, this causes a lot of stress on the structure and the motor.

**Note: The curves are shown separately, to better illustrate the point.**

On the other hand, if we use a polynomial trajectory, the curves look something like this:

<p align="center">
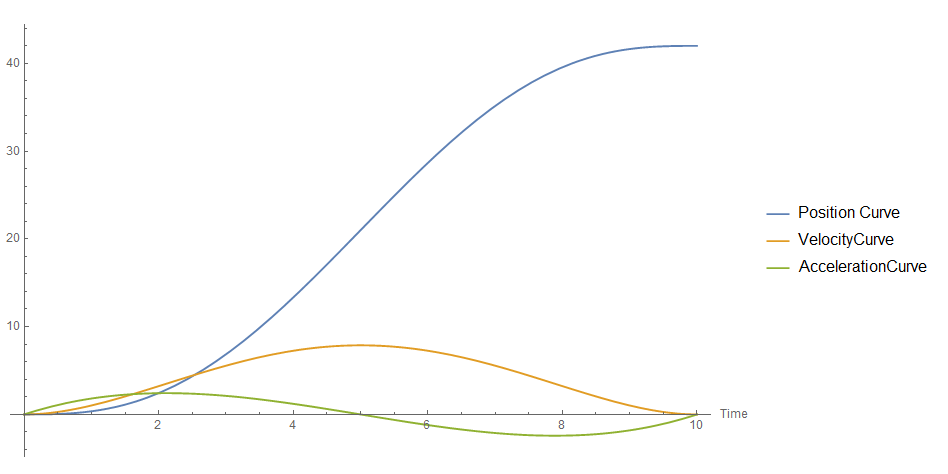
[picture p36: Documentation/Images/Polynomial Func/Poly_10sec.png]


</p>
As you can see here, the acceleration is less and the curve is much more gentle.
Of course, if you reduce the time a motion needs to be executed in a smaller time frame even with the polynomial trajectory you can have high accelerations, in those cases, you can either use other trajectories like trapezoidal or design the robot to handle higher stresses.

After doing some research on the topic, I decided to try to implement this. Luckily for me, such a project has already been attempted and I am very grateful to Joseph Q. Oberhauser for the work he has done on his [master thesis ](https://etd.ohiolink.edu/!etd.send_file?accession=ohiou1460045979&disposition=inline) which has a part that covers this exact topic. I am also grateful that he has uploaded his C# code to his [dropbox](https://www.dropbox.com/sh/l5rgy7s7osya5vz/AABrLWKVYxZhbu4hxOwEMSMZa?dl=0) and still has it available at the time of writing this documentation.
Even though it doesn't cover everything I needed, with the help of his work I was able to implement a working polynomial trajectory for my robot.
It is not the smoothest operation, but that is mostly since I am not using micro-stepping and because my stepper motors only have 200 steps per revolution. Those two things result in quite a bit of noise, but overall everything works as intended and there is a visible improvement in performance as the stepper motor doesn't skip steps and there is less force exerted on the structure.

##### [Back to top](#Contents)

---
### Diagrams
Due to the relative complexity of the system, I will not write too much text to explain it. Instead, I will use the things I learned in my Software Architectures course this semester to create diagrams for my system.

---

### System modules

<p align="center">

</p>

<p align="center">

</p>

##### [Back to top](#Contents)

---
### Deployment Structure
<p align="center">

</p>

##### [Back to top](#Contents)

---

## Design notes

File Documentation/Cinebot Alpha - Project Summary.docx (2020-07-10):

Assignment 1 | | Project Summary
Course | | Practical Robotics and Smart Things - 2020

Project author
№ | Pseudonym | | In person/online
1 | 4е 54 | | face-to-face

Project name | Cine-Bot α (CB-A1) ()

1. Short project description (Business needs and system features)

Cine-Bot α (CB-A1 for short) is a small camera controlling robot intended to be used for scale stop-motion animation/movie making.

CB-A1 aims to utilize the newest technologies in the IoT & robotics world.

CB-A1 is comprised of 2 parts, the robotic cine arm (RCA) and motion capture controller (MCC). Although the RCA itself will have a screen, the MCC is used to interface with the RCA remotely via a wireless connection. Via the MCC the operator can control every aspect of the RCA from the camera to motion programming. In the following section both components are discussed in more detail.

The hardware implementation as mentioned before is divided into two parts:

1. The RCA (server)
2. The Client – controller.

The RCA

The RCA is based on the Raspberry PI 4 4GB.

Sensors:

- Accelerometer – used for camera and arm control.
- Gyroscope – Used for camera tilt/rotate movement.
- Ultrasonic distance sensors – used for 360 collision detection during full manual mode (mode described later in the “Modes” section.
- Light sensor – used for operator feedback & automatic lighting adjustment.

Image/Video capture & lighting:

- Raspberry Pi Camera v2 – uses as primary image/video capture device.
- LED Array for scene lighting – used as a backup light source for the camera

User controls:

- Buttons - for motor jogging mode (testing motors directly from the robot)
- On/Off button

Actuators:

- Servo/stepper motors – used as primary control devices.

Modes of operation

1. Full manual – control comes directly from MCC.
2. Learn & repeat – control comes from MCC once and then the path is remembered and can be executed again.
3. Tracking auto – tracks object without ability for MCC control.
4. FrameX (auto after initial programming) – stop-motion mode. Follows path divided into frames, ideal for making a stop-motion sequence.

User interaction

The main way the user will interact with the system is either through the GUI directly on the RCA or through the MCC GUI.

Communication Between Modules

Via TCP.

2. Main Use Cases / Scenarios

Use case name | Brief Descriptions | Actors Involved
2.1. Select Mode | The User can browse the different modes that are available and select one. | All users
2.2. Start Execution | The user can start the execution if the full auto mode is enabled | All users
2.3. Jog Mode | The user can test if all of the motors are functional by pressing the buttons on the machine. | All users
2.4. Full Manual Mode | The user controls all of the parts of the robot arm. | All users
2.5. Learn and Repeat Mode | The user executes a path, the robot learns it and then repeats it. | All users
2.6. Tracking Auto | Tracks an object on the scene. | All users
2.7. FrameX | The users sets a path with waypoints the robots executes it while taking picture every n seconds. | All users

3. Renders/Project Visualizations (In development)

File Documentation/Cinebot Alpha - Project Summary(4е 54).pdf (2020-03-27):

1

Assignment 1 | Project Summary
Course | Practical Robotics and Smart Things - 2020

Project author
№ | Pseudonym | In person/online
1 | 4е 54 | face-to-face
Project name | Cine-Bot α (CB-A1) ()

### 1. Short project description (Business needs and system

features)

Cine-Bot α (CB-A1 for short) is a small camera controlling robot intended to be used for scale stop-motion animation/movie making. CB-A1 aims to utilize the newest technologies in the IoT & robotics world.

CB-A1 is comprised of 2 parts, the robotic cine arm (RCA) and motion capture controller (MCC). Although the RCA itself will have a screen, the MCC is used to interface with the RCA remotely via a wireless connection. Via the MCC the operator can control every aspect of the RCA from the camera to motion programming. In the following section both components are discussed in more detail.

The hardware implementation as mentioned before is divided into two parts:
1. The RCA
2. The MCC

### The RCA

The RCA is based on the Raspberry PI 4 4GB.

Sensors:
- Accelerometer – used for camera and arm control.
- Gyroscope – Used for camera tilt/rotate movement.
- Ultrasonic distance sensors – used for 360 collision detection during full manual mode (mode described later in the “Modes” section.

2

- Light sensor – used for operator feedback & automatic lighting adjustment.
Image/Video capture & lighting:
- Raspberry Pi Camera v2 – uses as primary image/video capture device.
- LED Array for scene lighting – used as a backup light source for the camera
User controls:
- LCD Touch screen - for user interaction
- Buttons - for motor jogging mode (testing motors directly from the robot)
- On/Off button

Actuators:
- Servo/stepper motors – used as primary control devices.

### The MCC

The MCC is also based on the Raspberry PI 4 4GB.

Sensors:
- Accelerometer – used to capture user motion in the X, Y, Z axes.
- Gyroscope – used to capture user rotation motion (tilt/pan)

User controls:
- LCD Touch screen - for user interaction
- On/Off button
- Servo for collision warning system – provides feedback to the user weather or not the RCA is about to hit an object.

### Modes of operation

1. Full manual – control comes directly from MCC.
2. Manual Stabilized – control comes from the MCC but is filtered to remove shaking from the operator.
3. Learn & repeat – control comes from MCC once and then the path is remembered and can be executed again.
4. Tracking semi-auto – can lock onto object but is controlled by MCC.

3

5. Tracking auto – tracks object without ability for MCC control.
6. FrameX (auto after initial programming) – stop-motion mode. Follows path divided into frames, ideal for making a stop-motion sequence.

### User interaction

The main way the user will interact with the system is either through the GUI directly on the RCA or through the MCC GUI.

### Communication Between Modules

(Currently being researched but it will likely be via UDP or Ad-hoc Wi-Fi

### 2. Main Use Cases / Scenarios

Use case name | Brief Descriptions | Actors Involved
2.1. Select Mode | The User can browse the different modes that are available and select one. | All users
2.2. Start Execution | The user can start the execution if the full auto mode is enabled | All users
2.3. Jog Mode | The user can test if all of the motors are functional by pressing the buttons on the machine. | All users
2.4. Full Manual Mode | The user controls all of the parts of the robot arm. | All users
2.5. Manual Stabilized Mode | The user controls all of the parts of the robot, but there is motion stabilization to remove tremors. (May not be included in final version) | All users
2.6. Learn and Repeat Mode | The user executes a path, the robot learns it and then repeats it. | All users
2.7. Tracking semi-auto Mode | Tracks an object while being controlled by the user. (May not be included in the final version.) | All users

4

2.8. Tracking Auto | Tracks an object on the scene. | All users
2.9. FrameX | The users sets a path with waypoints the robots executes it while taking picture every n seconds. | All users

### 3. Renders/Project Visualizations (In development)

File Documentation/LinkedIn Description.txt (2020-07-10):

This is my course project for the "Practical Robotics & Smart Things" course in FMI. It is my first robotics project and I am really excited to share it with you. Even though it is fairly simple, considering the current state of the field of robotics, it has been a truly eye-opening experience for me. It has shown me the career path I want to follow. 

You can find the full documentation on my Github page.

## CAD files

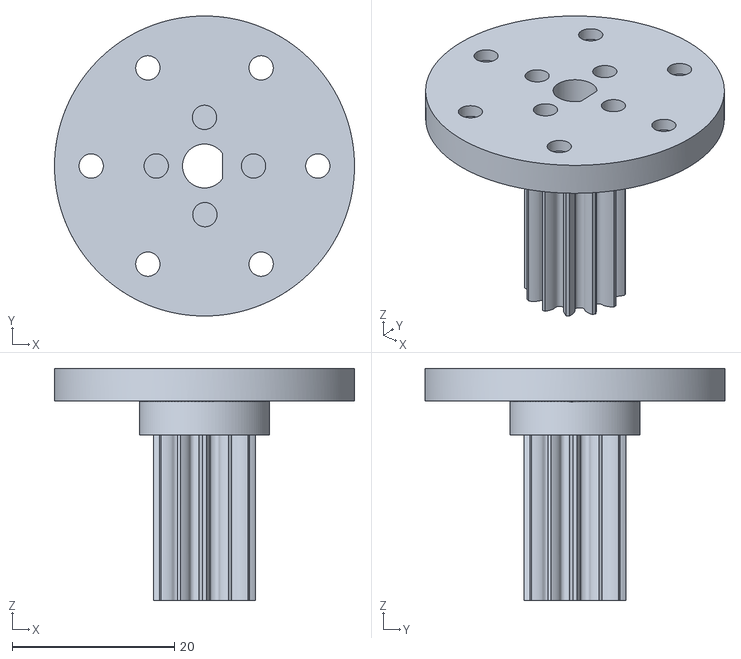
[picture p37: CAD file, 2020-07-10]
STL Files/Arm Joint/Sun_Gear_Bottom.stl
37.0 x 37.0 x 28.6

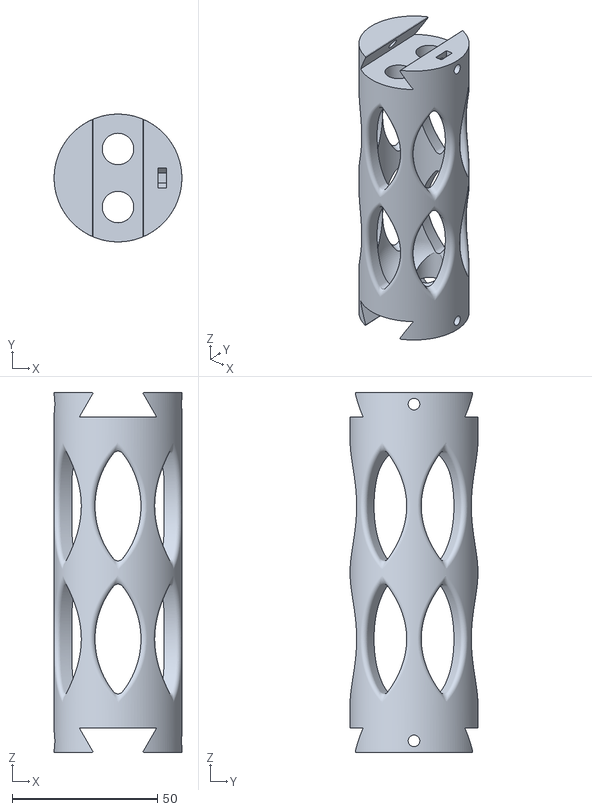
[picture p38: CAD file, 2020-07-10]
STL Files/Arm Sections/Arm_Section_Medium.stl
44.0 x 44.0 x 124.0

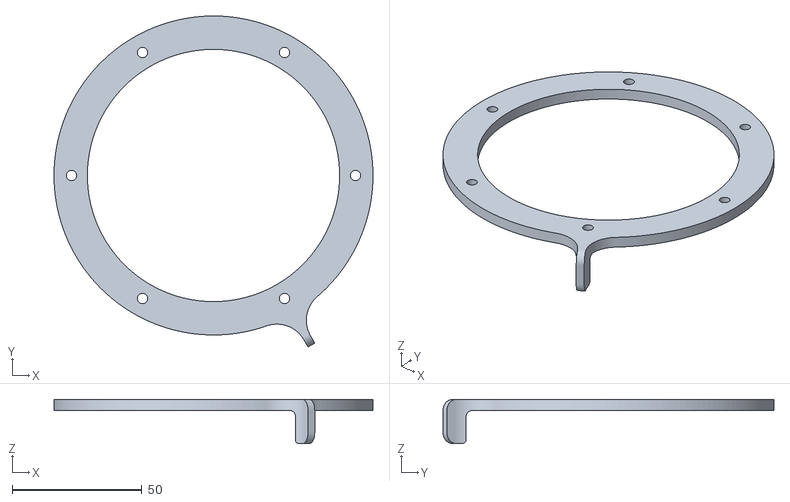
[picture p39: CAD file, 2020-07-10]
STL Files/Base & Base Drive/Limit_Switch_Trigger.stl
123.0 x 127.6 x 17.0

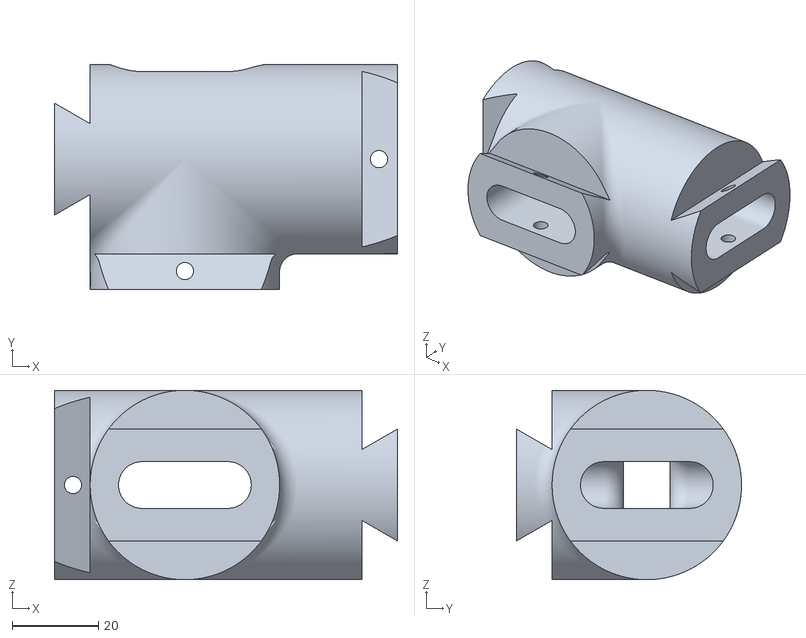
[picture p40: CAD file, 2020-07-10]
STL Files/Counterbalance/Gearbox Adapter.stl
79.7 x 52.3 x 44.0

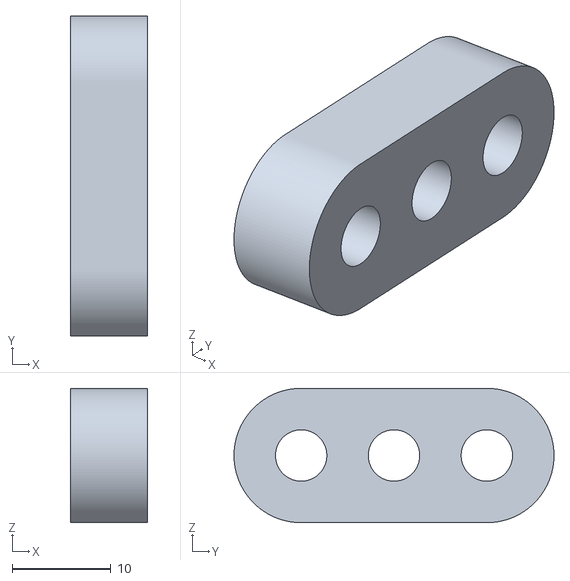
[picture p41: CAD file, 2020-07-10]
STL Files/Electronics Housing/Notification_Light_Panel.stl
7.80 x 32.4 x 13.6

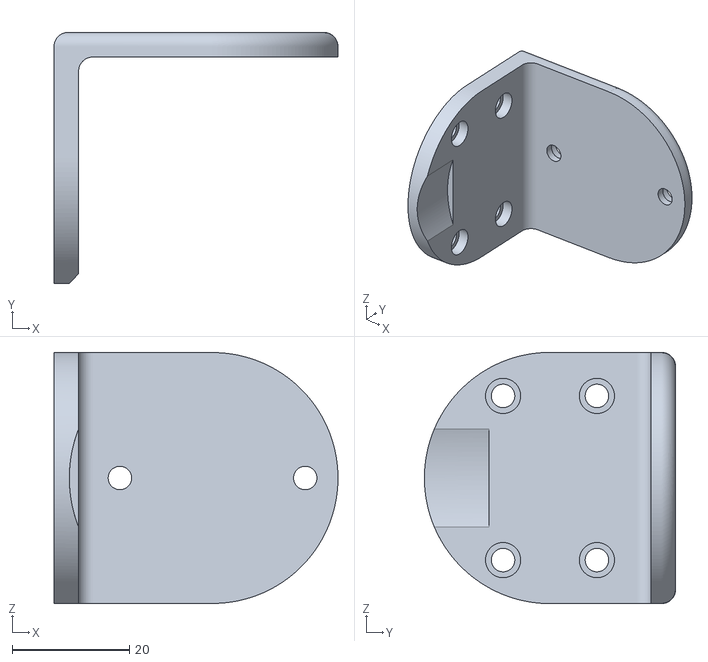
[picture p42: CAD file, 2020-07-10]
STL Files/Gimbal/Rotation_Arm.stl
48.4 x 42.8 x 42.8

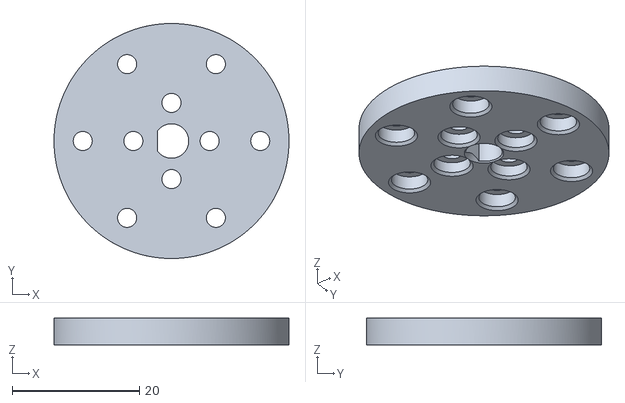
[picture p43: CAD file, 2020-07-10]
STL Files/Arm Joint/Sun_Gear_Top.stl
37.0 x 37.0 x 4.20

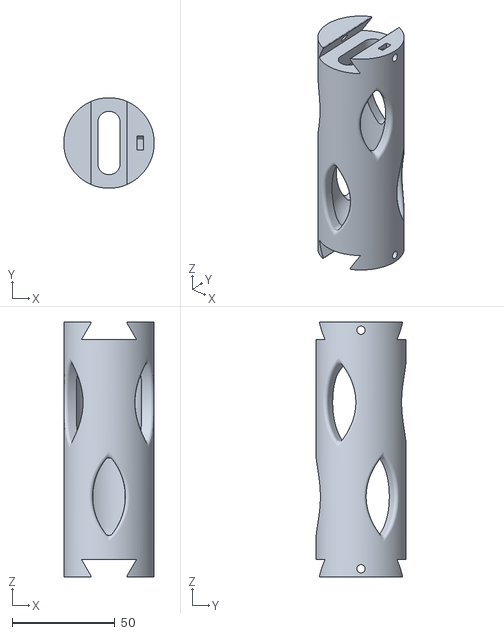
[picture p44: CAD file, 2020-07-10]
STL Files/Arm Sections/Arm_Section_Heavy.stl
44.0 x 44.0 x 124.0

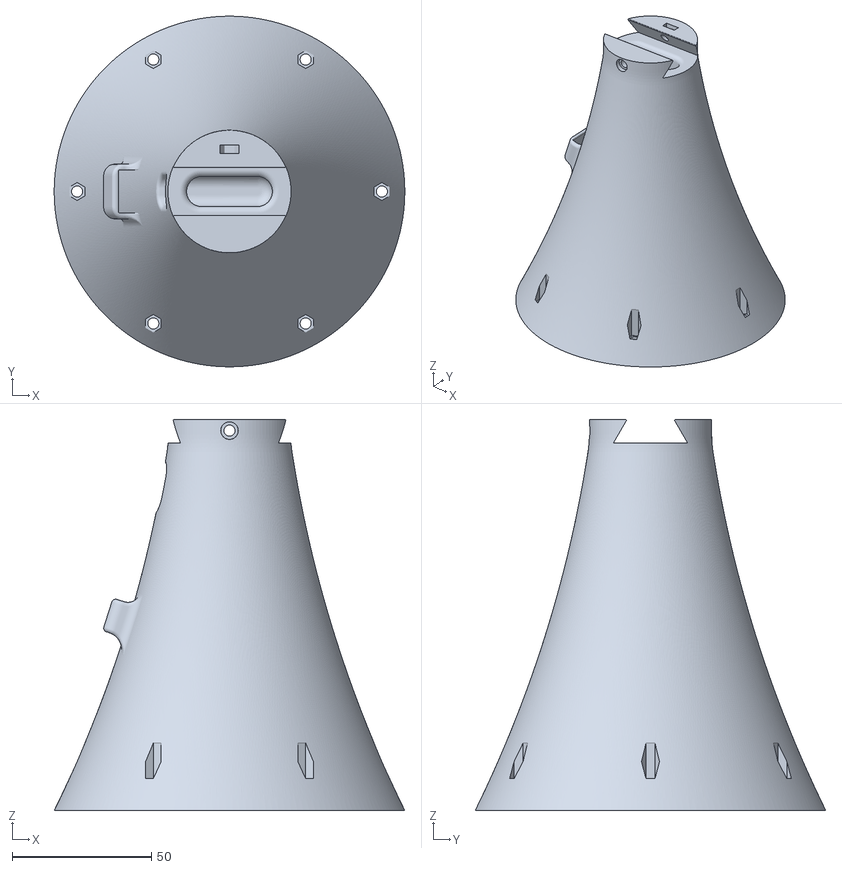
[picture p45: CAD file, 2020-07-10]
STL Files/Base & Base Drive/Base_Arm_Rework.stl
126.0 x 126.0 x 140.5

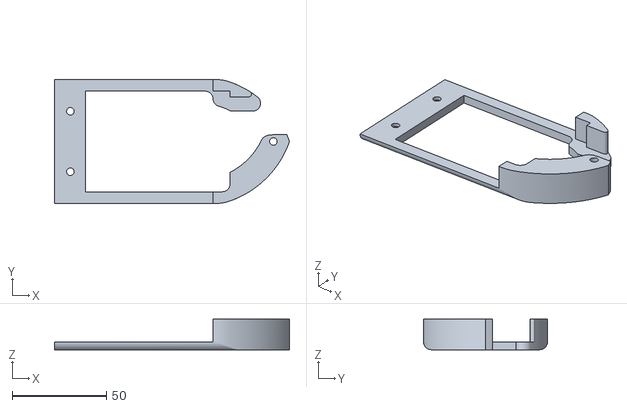
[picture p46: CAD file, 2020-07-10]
STL Files/Counterbalance/Arduino_Cover.stl
124.5 x 65.7 x 16.2

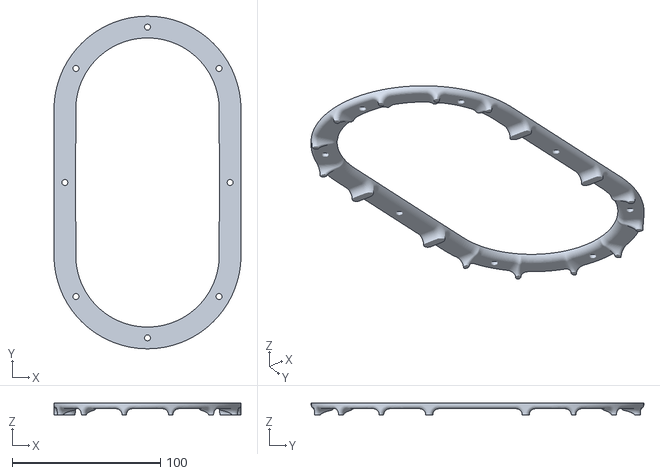
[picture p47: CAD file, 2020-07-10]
STL Files/Electronics Housing/Air_Intake Panel_Half.stl
126.2 x 224.5 x 8.00

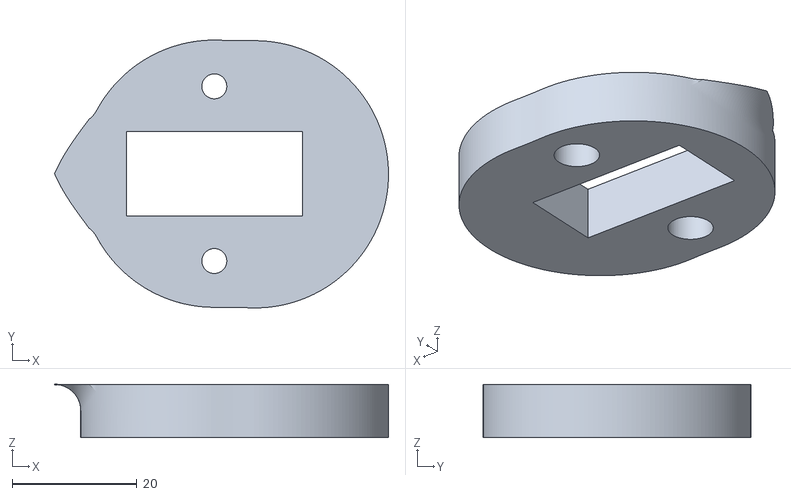
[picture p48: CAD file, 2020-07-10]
STL Files/Gimbal/Pan_Servo_Cover.stl
53.5 x 42.9 x 8.50

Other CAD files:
CAD Blueprints/Complete_Assembly.dwg
CAD Blueprints/Gimbal_Rev_3.dwg
CAD Blueprints/Part Evolution/Gimbal_Evolution.dwg
CAD Blueprints/Planetary_Gearbox_V2.1/Upgraded_Base_Drive v1.dwg
CAD Blueprints/Encoder_Mounting_Plate.dwg
CAD Blueprints/Planetary_Gearbox_V2.1/1 gearbox v3.dwg
CAD Blueprints/Arm_Joint.dwg
CAD Blueprints/Arm_Joint_recover.dwg
CAD Blueprints/Arm_Section.dwg
CAD Blueprints/CB-A1-V1.dwg
CAD Blueprints/Circuit_Board_Holders.dwg
CAD Blueprints/Electronics_Housing.dwg
CAD Blueprints/Encoder_Knob.dwg
CAD Blueprints/Gimbal.dwg
CAD Blueprints/Gimbal_recover.dwg
CAD Blueprints/Hardware_Library.dwg
CAD Blueprints/Planetary_Gearbox_V2.1/7t1GbV21.dwg
CAD Blueprints/Planetary_Gearbox_V2/7t1 Gearbox.dwg
CAD Blueprints/Robot_Base.dwg
CAD Blueprints/StopSwitch_Connector_Housing.dwg
CAD Blueprints/Worm_Gear/Design Accelerator/Worm Gear2.ipt
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

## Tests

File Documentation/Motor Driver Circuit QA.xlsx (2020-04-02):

Stepper Motor Driver Board QA Sheet
Driver lettering derived from PCB letters
Driver | Driver C |  | Driver D |  | Driver E
Status | Pass | Fail | Pass | Fail | Pass | Fail
3.3V Power Delivery
8V Power Delivery
3.3V Ground
8V Ground
Direction Control
Step Input
Driver Awake Input
Coil A Control
Coil B Control
Coil A LED
Coil B LED
Capacitor Connection

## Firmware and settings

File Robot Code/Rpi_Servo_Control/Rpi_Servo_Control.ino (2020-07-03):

//THIS WAS USED FOR THE DEMO LAST NIGHT
#include <Servo.h>
Servo panServo;
Servo rotationServo;
Servo tiltServo;

const byte numChars = 32;
String receivedChars;   // an array to store the received data
char targetServo;
bool gotTargetServo = false;
boolean newData = false;

void setup() {
    Serial.begin(9600);
    Serial.println("<Arduino is ready>");
    panServo.attach(9);
    rotationServo.attach(10);
    tiltServo.attach(11);

    panServo.write(75);
    rotationServo.write(80);
    tiltServo.write(80);
}

void loop() {
    recvWithEndMarker();
    showNewData();
}


void recvWithEndMarker() {
    static byte nextIndex = 0;
    char endMarker = '\n';
    char receivedChar;
   
    while (Serial.available() > 0 && newData == false) {
        receivedChar = Serial.read();
        if(!gotTargetServo)
        {
          targetServo = receivedChar;
          gotTargetServo=true;
        }
        else
        {
          if (receivedChar != endMarker) 
          {
            receivedChars+= receivedChar;
            nextIndex++;
            if (nextIndex >= numChars) {
                nextIndex = numChars - 1;
            }
          }
          else 
          {
            //receivedChars[nextIndex] = '\0'; // terminate the string
            nextIndex = 0;
            newData = true;
          }
        }      
    }
}

void showNewData() {
    if (newData == true) {
        
        int servoAngle = receivedChars.toInt();
        if(targetServo == 'P')
        {
            panServo.write(servoAngle);
            Serial.print("P"); 
        }

        if(targetServo == 'R')
        {
             rotationServo.write(servoAngle);
             Serial.print("R");
        }

        if(targetServo == 'T')
        {
          if(servoAngle > 125) 
          {
            servoAngle = 125;
          }
          tiltServo.write(servoAngle);
          Serial.print("T"); 
        }
               
        gotTargetServo=false;
        delay(45);
        Serial.print("Angle:");
        Serial.println(servoAngle);
        receivedChars = "";
        newData = false;
    }
}

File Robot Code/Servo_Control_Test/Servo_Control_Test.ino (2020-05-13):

int stepInput = 8;  // LED connected to digital pin 13
int servoControl = 9;    // pushbutton connected to digital pin 7
Servo rotateServo;
int servoPosition=0;
void setup() {
  pinMode(ledPin, OUTPUT);  
  pinMode(inPin, INPUT);
  rotateServo.attach(servoControl)
}

void loop() {
  piInput = digitalRead(stepInput);

  if(piInput == HIGH)
  {
    servoPosition++;
    rotateServo.write(servoPosition);
     delay(10);    
  }
}

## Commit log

2020-03-08 Added controller box & edited file structure
    [CB-A1-V1.dwg, rpi_MECH_4b_4p0-with_mounting.dwg, rpi_MECH_4b_4p0-with_mounting.dxf]
2020-03-11 Added Arm joint for stepper motor.
    [Arm_Joint.dwg, CB-A1-V1.dwg]
2020-03-13 Added Gimbal Mechanism
    [Arm_Joint.dwg, Arm_Joint_recover.dwg, Gimbal.dwg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]
2020-03-16 Added arm section, updated gimbal.
    [Arm_Joint.dwg, Arm_Section.dwg, Gimbal.dwg]
2020-03-16 Updated gimbal design.
    [Gimbal.dwg]
2020-03-20 Updates to Arm & Joint Sections
    [Arm_Joint.dwg, Arm_Section.dwg, Gimbal.dwg]
2020-03-20 Updated motor script
2020-03-21 Added Steppepr Gear Box
    [Arm_Joint.dwg]
2020-03-22 Updated arm section design
2020-03-22 Updated Gear Box Design
2020-03-22 Started planet gear design
2020-03-27 Updated blueprints.
    [Arm_Joint.dwg]
2020-03-29 Added base arm.
2020-03-29 Added gearbox mount.
2020-04-01 Added new 90deg arm adapter.
2020-04-02 Added Circuit Board Plates
    [Circuit_Board_Holders.dwg, Motor Driver Circuit QA.xlsx, Robot_Base.dwg]
2020-04-05 Updated Gimbal
    [Circuit_Board_Holders.dwg, Gimbal.dwg, Robot_Base.dwg]
2020-04-06 Added arm to gimbal connector.
    [Gimbal.dwg]
2020-04-14 Added Housing
    [Electronics_Housing.dwg]
2020-04-16 Preparing for final assembly rev 1
    [Complete_Assembly.dwg, Robot_Base.dwg]
2020-04-16 Working on complete assembly.
    [Hardware_Library.dwg]
2020-04-16 Setting up DH coords
    [Hardware_Library.dwg]
2020-04-17 Started worm drive development
    [Electronics_Housing.dwg, Worm Gear1.ipt, Worm Gear2.ipt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]
2020-04-21 Added worm gear assembly.
    [Gimbal.dwg]
2020-04-22 Updated worm gear
2020-04-29 Working on electronics housing.
2020-05-02 Completed Electronics Housing V1
2020-05-04 Added new gearbox, worked on robot code.
    [7t1 Gearbox.dwg, 7t1GbV21.dwg]
2020-05-05 Completed motor jog script, added collision detection for both joints.
2020-05-07 Added small planetary gearbox
    [1 gearbox v3.dwg, 7t1GbV21.dwg]
2020-05-09 Update gimbal Model
    [Gimbal_Rev_3.dwg]
2020-05-13 Completed basic servo control with rotary encoder.
2020-05-13 Blueprint edits.
    [Gimbal_Rev_3.dwg]
2020-05-14 Calibrated initial gimbal position.
2020-05-15 Working on motormanager update.
2020-05-15 Gimbal Blueprints update.
    [Gimbal_Rev_3.dwg]
2020-05-16 Servo Control Update
2020-05-16 Cad files metadata update.
2020-05-18 Updated servo control.
2020-06-07 Working on software & hardware
    [Arm_Joint.dwg, Gimbal.dwg, Gimbal_Evolution.dwg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]
2020-06-09 Working on final hardware components
    [Encoder_Knob.dwg, Encoder_Mounting_Plate.dwg, Gimbal_Rev_3.dwg]
2020-06-13 Testing camera
2020-06-14 Updating Blueprints
    [Gimbal_Rev_3.dwg]
2020-06-16 CAD Files Save
    [Encoder_Mounting_Plate.dwg]
2020-06-17 Testing Unix Domain Sockets (C#)
2020-06-17 Working on electronics housing V..2
2020-06-18 Working on electronics housing V.2
2020-06-18 Update electronics housing
2020-06-20 Working on updated motor control process.
2020-06-20 Updated blueprint files.
    [Gimbal_Rev_3.dwg]
2020-06-20 Improved emergency button functionality. Completed Multithread Stepper Control. Complete GTH function.
2020-06-25 Implemented polynomial velocity trajectory
2020-06-25 Improved bottom arm section of the robot.
2020-06-26 Added facial tracking with python and linked it with c# (needs calibration)
2020-06-29 Upgrading base drive
    [Upgraded_Base_Drive v1.dwg]
2020-06-30 Fixed limit switch logic.
2020-06-30 CAD Models Save
2020-07-03 Completed simple stepper jog mode
2020-07-03 Completed limit switch logic.
2020-07-03 CAD save
2020-07-03 Created encoder class. Preparing for path follow implementation
2020-07-03 Completed gimbal homing sequence.
2020-07-05 Adding schematics.
    [Stepper Motor Connection Schematic.fzz]
2020-07-05 Update Stepper Motor Connection Schematic.png
2020-07-05 Update encoder schematic.
    [Button and Encoder Connections Schematic.fzz]
2020-07-06 Added STL Files folder
    [Button and Encoder Connections Schematic.fzz, Encoder Knob V1.stl]
2020-07-06 Added media materials to documentation
2020-07-07 Update motor manager to add poly movement option.
2020-07-08 Added CAD Models
2020-07-09 Added LED notification pattern.
2020-07-09 Added universal connector image
2020-07-10 Added STL files
    [Air_Intake Panel_Half.stl, Arduino_Cover.stl, Arduino_Mount.stl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]
2020-07-12 Calibrating facial tracking.
2020-07-12 Update Button and Encoder Connections Schematic.fzz
    [Button and Encoder Connections Schematic.fzz]
2020-07-13 Updated electronics schematics.
    [Button and Encoder Connections Schematic.fzz]
